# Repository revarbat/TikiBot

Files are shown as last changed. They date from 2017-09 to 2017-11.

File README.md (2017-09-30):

TikiBot
=======
Touchscreen BarBot software for auto-dispensing mixed drinks.  Runs under
Linux on a Raspberry Pi or Udoo, using DC motor controllers over I2C, to
activate pumps and valves to dispense ingredients.

TikiBot Lives!  It was a great success at my friend's Tiki themed party.

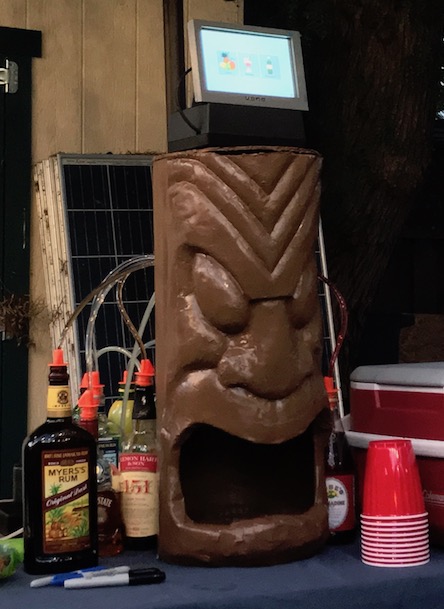
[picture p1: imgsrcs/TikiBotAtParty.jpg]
TikiBot Live at a Party


Standard Drinks List
--------------------
The default configuration is for a 12-feed TikiBot.
It expects the following ingredient feeds:

1. Meyer's Dark Rum
2. Appleton's Signature Blend
3. Meyer's Platinum White Rum
4. Lemonheart 151 Rum
5. Lime Juice
6. Lemon Juice
7. Orange Juice
8. Pineapple Juice
9. Passion Fruit Syrup
10. Sugar Syrup
11. Angostura Bitters
12. Grenadine

The following Tiki recipes can be made from those:

1. Beachcomber's Gold
2. Chief Lapu Lapu
3. Hurricane
4. Planter's Punch
5. Shrunken Skull
6. Tiger Shark
7. Trader Vic Grog
8. Zombie

The following non-alcoholic juice drinks can also be made:

1. Orange Juice
2. Pineapple Juice
3. Pineapple Orange Juice
4. Tropical Punch

Hardware
--------
This software has been tested with the following hardware:

- Udoo Neo ( [Udoo.org](https://www.udoo.org) )
- 7" 800x480 Touchscreen HDMI display
- 3 Adafruit DC Motor Featherwings ( [Adafruit.com](https://www.adafruit.com/product/2927) )
- 12 Small self-priming pumps ( [TrossenRobotics.com](http://www.trossenrobotics.com/robotgeek-pump-small) )
- 12 Normally Closed solonoid valves ( [Amazon.com](https://www.amazon.com/dp/B007D1U64E/ref=cm_sw_r_tw_dp_x_qDVWzbPCEW4K5) )

Each DC Motor controller handles up to 4 feeds.  Each motor controller will
need to have a consecutive different I2C address. You can alternately use
the following DC motor controllers without changing any code:

- Adafruit DC & Stepper Motor HAT for Raspberry Pi ( [Adafruit.com](https://www.adafruit.com/product/2348) )
- Adafruit Motor/Stepper/Servo Shield for Arduino v2 ( [Adafruit.com](https://www.adafruit.com/product/1438) )

It should be trivial to use a Raspberry Pi instead of the Udoo Neo.
Probably the easiest configuration would be to use a Raspberry Pi
with a few stacked DC Motor HATs.

Each feed is a paired pump and valve, wired in parallel.
Each pump/valve combo should be wired and plumbed as follows:

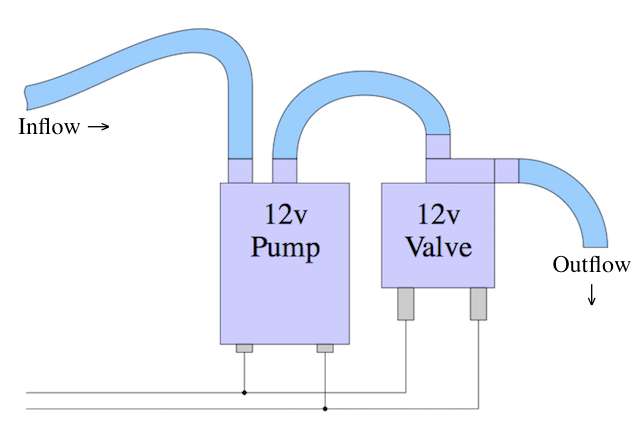
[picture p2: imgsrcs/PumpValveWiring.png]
Pump/Valve wiring


The polarity of the wiring is irrelevant for the linked pumps and
valves.  For them, either polarity will result in the forward pump
action with the valve open.

The pumps-valve pairs can be seated into a ring of Pump Wedges that can
be 3D printed from the model `STLs/PumpWedge12.stl` (for a 12 feed ring)
or `STLs/PumpWedge16.stl` (for 16 feed rings).  A corresponding Feed Guide
model can be found as `STLs/FeedGuide12.stl` or `STLs/FeedGuide16.stl`.
The feed guide has a slot in the bottom that can hold a funnel for all
the feeds to pour and mix into, which will drain into the target glass
or cup.

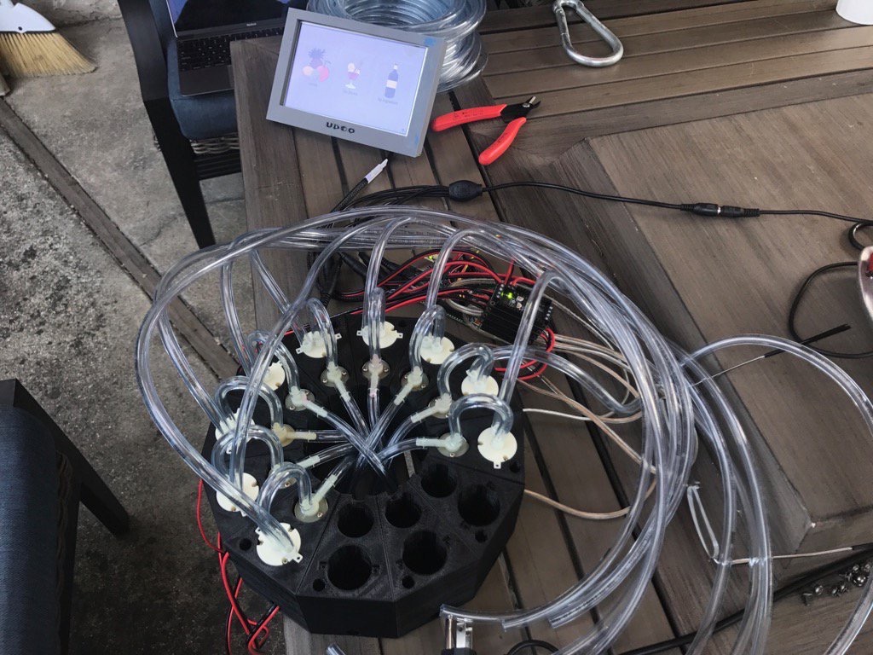
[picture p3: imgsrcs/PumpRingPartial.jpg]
Pump/Valve Ring, Partially Completed


Installation
------------

    unzip TikiBot.zip
    cd TikiBot
    pip3 install -r requirements.txt

Running TikiBot
---------------
`gui.py` is the main file to run to launch this application.  You will
need to run it using Python 3.6 or better.

     cd TikiBot/TikiBot
     python3 gui.py

Configuration
-------------
The file `TikiBot/resources/tikibot_configs.yaml`: Contains all configs
for passcode, feeds, recipes, etc. for a standard set of Tiki drinks.
On first run, if you edit any configs on the configuration screen,
these configs will be written out to the file `$HOME/.tikibot.yaml`,
which will be read in all future runs.

In the lower right corner of the main screen is a gear icon.  This is
the configuration menu button. If you press it, it will ask for an
administrative passcode.  The default is '8888'.  Once you enter the
correct passcode, you will be shown the configuration screen.  From
here, you can change the passcode (recommended!), add, edit and re-order
feeds, add, and edit drink recipes, and shutdown or reboot the system.
Any changes made here will be saved to the `$HOME/.tikibot.yaml` file.

Calibration
-----------

1. Enter the configuration screen as described above.

2. In the configuration screen, the `Manage Feeds` button will show you
    all of the feeds that the software expects, in the order that it
    expects them.

3. Take an empty cup and zero a gram scale with it on it.  Make sure the
    scale is set to measure grams.

4. Select a feed, and you will be presented with a screen that will let
    you rename it, enable/disable it, start and stop it manually, and
    calibrate it.

5. Make sure that the feed line you selected has the expected ingredient
    attached.

6. Place the cup under the output of the feed.

7. Press the `Start Feed` button to prime the feedline.

8. When fluid starts pouring into the cup, press the `Stop Feed` button.

9. Pressing the calibration button will show you a screen which will let
    you calibrate the flow rate and pulse overage for that feed.

10. Start with a Pulse overage of 0.2 and a Duty cycle of 100%.  Those
    are only really needed for advanced calibration.  Select an amount
    of 25 milliliters to dispense.  A flow rate of 12.0 is a reasonable
    starting place.

11. Empty the cup and re-zero the scale with the empty cup.

12. Place the cup back under the output of the feed.

13. Press `Pour` to dispense into the cup.  Wait for it to finish dispensing.

14. Weigh the cup, to see how many grams of fluid were dispensed.

15. Take the number of grams measured, divide it by the expected number of
    milliliters dispensed (25mL, if you followed the above instructions),
    then multiply that by the current `Flow` setting.  Change the `Flow`
    to this new value.

    `newflow = oldflow * dispensed / expected`

    Note: You can expect viscous fluids like Sugar Syrup to have very low
    flow rates like 2.5 mL/s.

16. Repeat steps 11 to 15 a couple times until the amount dispensed is
    within about a gram of the expected amount.

17. Press the back arrow button to get back to the feeds listing screen.

18. Select the next feed button and go back to step 3.  Repeat until all
    feeds have been calibrated.

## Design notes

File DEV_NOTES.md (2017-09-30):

Developer Notes
===============

Screens Concept
---------------
The touchscreen user interface is based around the idea of a stack
of screens, something like old HyperCard.

- `screen_push(newscreen)`:
    pushes a new screen onto the stack.

- `screen_pop()`:
    pops the topmost screen off of the stack.

- `activate()`:
    This method called on a screen class when that screen
    becomes the topmost screen, either through push or pop.
    This allows for updating the content of the screen after
    another screen has been popped off the top of the stack.

Touchscreen Widgets
-------------------
These are widgets that can be used in the creation of a screen.

- RectButton
    Provides a rectangular button on all platforms.

- TouchCheckbox:
    Provides a slider-switch visual version of the standard
    CheckButton.  Slightly prettier and more touchscreen friendly.

- TouchSpinner:
    Provides a basic increment/decrement Spinner widget that is
    more touchscreen friendly.

Generic Screens
---------------
There's a few generic screens that are used in multiple places:

- SelectScreen:
    Given a list of strings, shows buttons for each one, with
    a callback that gets passed the text of the button pressed.
    This is sometimes used as a confirmation screen by just giving
    it a ["Confirm"] button and a text message to display.

- AlphaScreen:
    Provides a touchscreen keyboard for text entry and editing.

- ListScreen:
    Provides a way to edit a list of arbitrary size, through callbacks.
    Can add, delete, edit, and re-order items with standard buttons.

- NotifyScreen:
    Displays a message for the user to see and dismiss.

- LockScreen:
    Dispays a numeric keypad to allow entry or setting of keycodes.

Screens Layout
--------------
Here's the hierarchy of GUI screens for the application.  The button
name that leads to a screen is in "quotes".  If a screen is a
subclass of another screen class, the base class is in (parens).

    MainScreen
        "Juices" RecipeScreen(SelectScreen)
            PourScreen
                "Pour" DispensingScreen
        "Tiki Drinks" RecipeScreen(SelectScreen)
            PourScreen
                "Pour" DispensingScreen
        "By Ingredient" ByIngredientScreen(SelectScreen)
            PourScreen
                "Pour" DispensingScreen
        "⚙" LockScreen
            ConfigScreen
                "Manage Feeds" ManageFeedsScreen(ListScreen)
                    "+" AlphaScreen
                        "Select" FeedEditScreen
                            "Rename Feed" AlphaScreen
                            "Calibrate" CalibScreen
                    "-" SelectScreen
                    "✎" FeedEditScreen [see above]
                "Manage Recipes" ManageRecipesScreen(ListScreen)
                    "+" AlphaScreen
                        "Select" RecipeEditScreen
                            "Recipe:" AlphaScreen
                            "Category:" AlphaScreen
                            "+" SelectScreen
                            "-" SelectScreen
                            "✎" AmountScreen
                    "-" SelectScreen
                    "✎" RecipeEditScreen [see above]
                "Dump All Feeds" DumpScreen
                "Change Passcode" LockScreen
                    NotifyScreen
                "Shutdown" ShutdownScreen

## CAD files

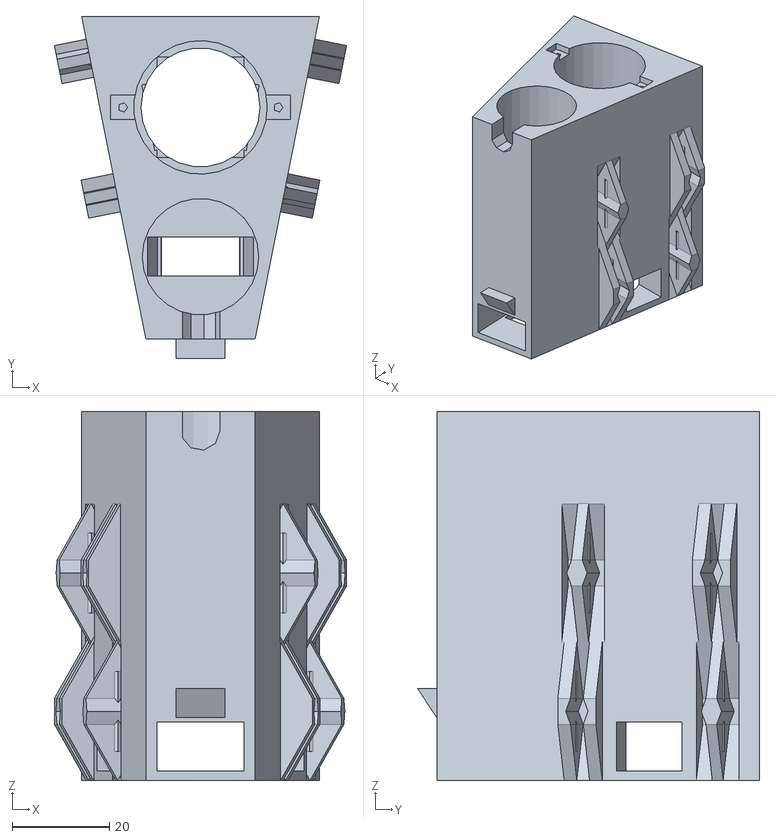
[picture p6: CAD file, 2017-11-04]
STLs/PumpWedge16.stl
60.2 x 70.5 x 76.0

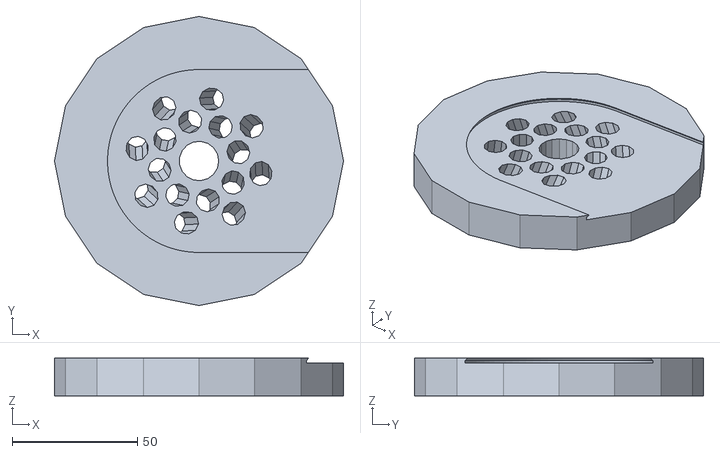
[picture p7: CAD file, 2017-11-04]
STLs/FeedGuide16.stl
115.3 x 115.3 x 15.0

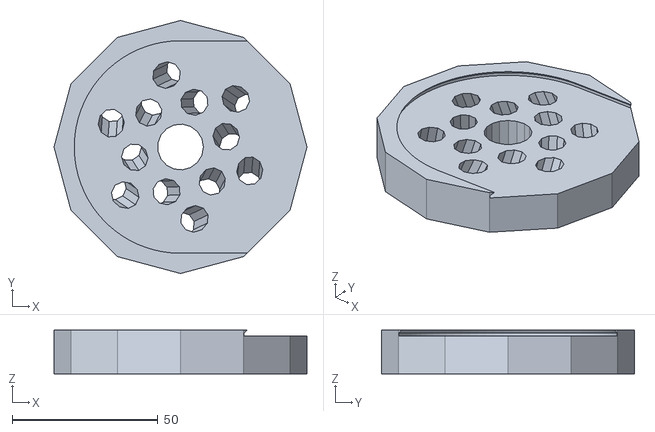
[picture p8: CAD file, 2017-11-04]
STLs/FeedGuide12.stl
86.9 x 86.9 x 15.0

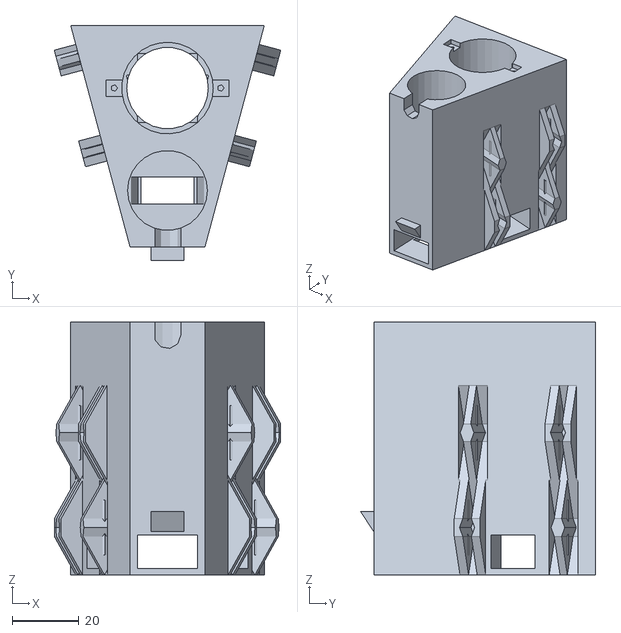
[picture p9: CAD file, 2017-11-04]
STLs/PumpWedge12.stl
68.0 x 70.5 x 76.0

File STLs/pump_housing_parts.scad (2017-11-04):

use <BOSL/transforms.scad>
use <BOSL/shapes.scad>
use <BOSL/joiners.scad>


/* [General] */

// Which part to print.
parts = "feedguide"; // [assembled:Full Assembly,feedguide:Output Feed Guide,ringseg:Ring Segment,stand:Standoff Pillars]

// Thickness of walls in mm.
wall_thick = 5; // [2:0.5:10]

// Number of pumps in the ring.
pump_count = 12; // [4:1:24]

tubing_diam = 9;

stand_height = 200;


/* [Pump] */

// Diameter of pump body, in mm.
pump_diam = 27.5; // [20:0.5:75]

// Diameter of pump inlet, in mm.
pump_inlet_diam = 8; // [3:0.5:10]

// Diameter of pump outlet, in mm.
pump_outlet_diam = 8; // [3:0.5:10]

// Offset of pump outlet, in mm.
pump_outlet_offset = 9.5; // [3:0.5:35]

// Offset of pump outlet, in mm.
pump_outlet_angle = 0; // [0:15:345]

// Length of pump, in mm.
pump_length = 61.0; // [20:0.5:100]

// Size of pump screws in mm.
pump_screw_size = 2.0; // [2:5]

// Size of pump screws in mm.
pump_screw_spacing = 32.0; // [20:0.5:75]


/* [Valve] */

// Diameter of valve body, in mm.
valve_diam = 24; // [16:0.5:75]

// Diameter of valve inlet, in mm.
valve_inlet_diam = 8; // [3:0.5:10]

// Diameter of valve outlet, in mm.
valve_outlet_diam = 8; // [3:0.5:10]

// Offset of valve outlet, in mm.
valve_outlet_offset = 9.5; // [3:0.5:35]

// Offset of valve outlet, in mm.
valve_outlet_angle = 0; // [0:15:345]

// Length of valve, in mm.
valve_length = 37.0; // [20:0.5:100]




/* [Hidden] */

pi = 3.141592653589793236;

slop = 0.2;


$fa = 3;
$fs = 3;


wedge_height = max(pump_length, valve_length) + wall_thick + 10;
wedge_width = max(pump_diam, valve_diam) - wall_thick;
wedge_depth = pump_diam+valve_diam+3*wall_thick;

module pump_housing_ring_segment()
{
	h = wedge_height;
	w = wedge_width;
	d = wedge_depth;
	ow = w + d * 2 * tan(360/pump_count/2);
	joiner_height = h * 0.75;
	union() {
		difference() {
			union() {
				// Main wedge shape.
				up(h/2) xrot(-90) trapezoid([w, h], [ow, h], h=d, center=true);

				// Feed guide support
				up(10+2+1) fwd(d/2) trapezoid([10, 0.1], [10, 2*4], h=6, center=false);
			}

			// side joiner clearing
			up(joiner_height/2) {
				yrot_copies([0, 180]) {
					right(w/2) {
						fwd(d/2) {
							zrot(-360/pump_count/2) {
								back(d/2-wall_thick/2) {
									zrot(90) joiner_clear(h=joiner_height, w=8, clearance=1);
									back(d/2-wall_thick) zrot(-90) yrot(180) joiner_clear(h=joiner_height, w=8, clearance=1);
								}
							}
						}
					}
				}
			}

			// radial wiring holes
			up(2) upcube([valve_diam-2*3, d+1, 10], center=true);

			// Pump hole
			back(d/2-pump_diam/2-wall_thick) {
				// Diametral wiring holes
				up(2) {
					xflip_copy() {
						zrot(360/pump_count/2) {
							left(ow/2) upcube([ow, pump_diam/2, 10]);
							left(pump_diam/2-4) {
								up(10-0.01) trapezoid([2*3, pump_diam/2], [0.1, pump_diam/2], h=5, center=false);
							}
						}
					}
				}

				// radial wiring hole taper
				up(10+2-0.01) trapezoid([valve_diam-2*3, pump_diam-2], [valve_diam-2*3, pump_diam-2*5], h=5, center=false);

				// Pump Body hole
				up(h-pump_length+0.01) {
					cylinder(h=pump_length, d=pump_diam, center=false);
					cylinder(h=h*3, d=pump_diam-3, center=true);
				}

				// Pump Tabs
				up(h-2+0.01) {
					xspread(pump_screw_spacing) {
						upcube([pump_screw_size*2.5, pump_screw_size*2.5, 2]);
					}
				}

				// Pump tab screw holes
				up(h-15+0.01) {
					xspread(pump_screw_spacing) {
						cylinder(d=pump_screw_size, h=16, center=false);
					}
				}
			}

			// Valve hole
			fwd(d/2-valve_diam/2-wall_thick) {
				// Valve body hole and shelf.
				up(h-valve_length+0.01) cylinder(h=valve_length, d=valve_diam, center=false);
				down(0.01) trapezoid([valve_diam-8, 10], [valve_diam-2, 8], h=h-valve_length+1, center=false);

				// Valve output clearance
				up(h-valve_outlet_diam/2) {
					up(5/2) {
						hull() {
							zspread(5) {
								xrot(90) cylinder(d=valve_outlet_diam, h=valve_diam, center=false);
							}
						}
					}
				}
			}
		}

		// Side Joiners
		up(joiner_height/2) {
			yrot_copies([0,180]) {
				right(w/2) {
					fwd(d/2) {
						zrot(-360/pump_count/2) {
							back(d/2-wall_thick/2) {
								zrot(-90) joiner(h=joiner_height, w=8, l=6);
								back(d/2-wall_thick) zrot(-90) yrot(180) joiner(h=joiner_height, w=8, l=6, slop=slop);
							}
						}
					}
				}
			}
		}
	}
}
//!pump_housing_ring_segment();



module pump_housing_feed_guide()
{
	h = 15;
	w = wedge_width;
	d = wedge_depth;
	funnel_diam = 75;
	r = w / 2 / sin(180/pump_count);
	difference() {
		// Main body.
		cylinder(r=r, h=h, center=false, $fn=pump_count);

		// Central stacking bank bypass.
		cylinder(d=tubing_diam*1.75, h=h*3, center=true);

		// Inner ring of feeds.
		zring(n=pump_count/2, r=tubing_diam*2.0) {
			yrot(-10) xrot(-15) cylinder(d=tubing_diam, h=h*3, center=true);
		}

		// Outer ring of feeds.
		zrot(360/(pump_count/2)/2) {
			zring(n=pump_count/2, r=tubing_diam*3.0) {
				yrot(-10) xrot(-20) cylinder(d=tubing_diam, h=h*3, center=true);
			}
		}

		// funnel groove
		hull() {
			grid_of(xa=[0, 2*r]) {
				up(h-2) {
					cylinder(h=1.01, d=funnel_diam, center=false);
					up(1) cylinder(h=1.01, d1=funnel_diam, d2=funnel_diam-2*1, center=false);
				}
			}
		}
	}
}



module pump_housing_stand()
{
	h = stand_height * ((stand_height>150)? 0.5 : 1.0);
	w = wedge_width;
	d = wedge_depth;
	joiner_height = h * 0.75;
	union() {
		difference() {
			union() {
				cylinder(h=h, d=pump_diam+6, center=false);
				cylinder(h=h+12, d=pump_diam-3-slop, center=false);
			}
			down(0.01) {
				cylinder(h=h*2, d=pump_diam-10, center=false);
				difference() {
					cylinder(h=h-10+0.02, d=pump_diam-3, center=false);
					upcube([10-slop, d, 10-slop]);
				}
				up(h-10) {
					cylinder(h=7, d1=pump_diam-3, d2=pump_diam-10, center=false);
				}
			}
			up(10/2-0.01) {
				xrot(-90) upcube([10, 10, d]);
			}
			up(h) {
				upcube([10-slop, d, 20]);
			}
		}
	}
}



module pump_housing_parts() { // make me
	h = wedge_height;
	w = wedge_width;
	d = wedge_depth;
	r = w / 2 / sin(180/pump_count) + d/2;
	if (parts == "assembled") {
		zring(r=r, n=pump_count, rot=true) {
			zrot(-90) pump_housing_ring_segment();
		}
		up(22+10+2+1) {
			zrot(360/pump_count/2) yrot(180) pump_housing_feed_guide();
		}
	} else if (parts == "ringseg") {
		pump_housing_ring_segment();
	} else if (parts == "feedguide") {
		pump_housing_feed_guide();
	} else if (parts == "stand") {
		pump_housing_stand();
	}
}



pump_housing_parts();



// vim: noexpandtab tabstop=4 shiftwidth=4 softtabstop=4 nowrap

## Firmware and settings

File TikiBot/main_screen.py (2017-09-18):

try:  # Python 2
    from Tkinter import *  # noqa
except ImportError:  # Python 3
    from tkinter import *  # noqa

import math
from recipes import Recipe
from rectbutton import RectButton
from recipe_screen import RecipeScreen
from lock_screen import LockScreen
from config_screen import ConfigScreen
from byingredient_screen import ByIngredientScreen


class MainScreen(Frame):
    def __init__(self, master):
        super(MainScreen, self).__init__(master, class_="MainScreen")
        self.master = master
        self.buttons = []
        self.update_buttons()

    def update_buttons(self):
        for btn in self.buttons:
            btn.forget()
            btn.destroy()
        types = Recipe.getTypeNames()
        colsarr = [1, 2, 3, 2, 3, 3, 4]
        maxcols = colsarr[len(types)]
        col, row = 1, 1
        for type_ in types:
            img = self.master.get_image(Recipe.getTypeIcon(type_))
            cmd = lambda typ=type_: self.handle_type_button(typ)
            btn = Button(self, text=type_, compound=TOP, image=img, command=cmd, width=160)
            btn.grid(column=col, row=row, padx=5, pady=5)
            self.buttons.append(btn)
            col += 1
            if col > maxcols:
                col = 1
                row += 1
                self.rowconfigure(row, weight=0)
        img = self.master.get_image("IngredientsIcon.gif")
        btn = Button(self, text="By Ingredient", compound=TOP, image=img, command=self.handle_button_ingredients, width=160)
        btn.grid(column=col, row=row, padx=5, pady=5)
        self.buttons.append(btn)
        confbtn = RectButton(self, text="\u2699", command=self.handle_button_conf, width=15, height=20)
        confbtn.grid(column=maxcols, row=row, columnspan=2, rowspan=2, sticky=S+E)
        self.buttons.append(confbtn)
        self.columnconfigure(0, weight=1)
        for col in range(maxcols):
            self.columnconfigure(col+1, weight=0)
        self.columnconfigure(maxcols+1, weight=1)
        self.columnconfigure(maxcols+2, weight=0)
        self.columnconfigure(maxcols+3, weight=0)
        self.rowconfigure(0, weight=1)
        self.rowconfigure(1, weight=0)
        self.rowconfigure(row+1, weight=1)
        self.rowconfigure(row+2, weight=0)
        self.rowconfigure(row+3, weight=0)

    def activate(self):
        self.update_buttons()

    def handle_type_button(self, type_):
        recipes = Recipe.getRecipesByType(type_)
        self.master.screen_push(RecipeScreen(self.master, recipes, "Choose one of these %s:" % type_))

    def handle_button_ingredients(self):
        self.master.screen_push(ByIngredientScreen(self.master))

    def handle_button_conf(self):
        self.master.screen_push(LockScreen(self.master, ConfigScreen(self.master)))

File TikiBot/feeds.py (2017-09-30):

import sys
import time
import platform
import operator

from Adafruit_MotorHAT import Adafruit_MotorHAT as AFMH
from Adafruit_GPIO.I2C import get_i2c_device


progstart_time = time.time()


def eprint(*args, **kwargs):
    print(*args, file=sys.stderr, **kwargs)


class SupplyFeed(object):
    motor_controllers = {}
    dc_motors = {}
    max_motor_num = 0
    feed_order = []
    feeds = {}
    feed_types = {}

    def __init__(self, type_, name, flowrate=14.2, overage=0.25, proof=0, avail=True):
        if type_ not in SupplyFeed.feed_types:
            SupplyFeed.feed_types[type_] = []
        SupplyFeed.feed_types[type_].append(self)
        self.type_ = type_
        self.name = name
        self.flowrate = flowrate
        self.pulse_overage = overage
        self.proof = proof
        self.flowing = False
        self.avail = avail
        self.motor_num = SupplyFeed.max_motor_num
        self.motor = None  # Defer instantiation for cross-platform debugging
        SupplyFeed.max_motor_num += 1
        SupplyFeed.feeds[name] = self
        SupplyFeed.feed_order.append(self)

    @classmethod
    def fromDict(cls, d):
        """Create new SupplyFeed instances from a dictionary description."""
        # Delete old feeds
        for feed in cls.feed_order:
            feed.delete_feed()
        # Add feeds from dict
        for feeddict in d['feeds']:
            for name, data in feeddict.items():
                cls(
                    data.get('type', 'Juices'),
                    name,
                    flowrate=data.get('flowrate', 14.2),
                    overage=data.get('overage', 0.25),
                    proof=data.get('proof', 0),
                    avail=data.get('available', True)
                )

    @classmethod
    def toDictAll(cls, d):
        """Create a dictionary description of all SupplyFeed instances."""
        d['feeds'] = []
        for feed in cls.feed_order:
            d['feeds'].append(feed.toDict())
        return d

    def toDict(self):
        """Create a dictionary description of this SupplyFeed instance."""
        return {
            self.name: {
                'type': self.type_,
                'flowrate': self.flowrate,
                'overage': self.pulse_overage,
                'proof': self.proof,
                'available': self.avail,
            }
        }

    @classmethod
    def _getMotorByNumber(cls, motor_num):
        """Returns the DCMotor instance for the given motor number."""
        addr = 0x60 + motor_num // 4
        num = motor_num % 4
        if addr not in cls.motor_controllers:
            busnum = 0
            if platform.system() == "Linux":
                if "udooneo" in platform.release():
                    busnum = 1
            cls.motor_controllers[addr] = AFMH(addr, i2c_bus=busnum)
        if motor_num not in cls.dc_motors:
            cls.dc_motors[motor_num] = cls.motor_controllers[addr].getMotor(num + 1)
        return cls.dc_motors[motor_num]

    @classmethod
    def getTypeNames(cls):
        """Returns a sorted string list of all SupplyFeed types."""
        return sorted(cls.feed_types.keys())

    @classmethod
    def getFeedsByType(cls, name):
        """Returns a list of all SupplyFeeds of a given type, sorted by name."""
        feed_list = cls.feed_types[name]
        return sorted(feed_list, key=operator.attrgetter('name'))

    @classmethod
    def getNames(cls):
        """Returns a sorted list of the names of all SupplyFeeds."""
        return sorted(cls.feeds.keys())

    @classmethod
    def getAll(cls):
        """Returns a list of all SupplyFeeds, sorted by name."""
        for key in sorted(cls.feeds.keys()):
            yield cls.feeds[key]

    @classmethod
    def getAllOrdered(cls):
        """Returns a list of all SupplyFeeds, sorted by feed number."""
        return cls.feed_order

    @classmethod
    def getByName(cls, name):
        """Get a SupplyFeed instance by name."""
        return cls.feeds[name]

    def getName(self):
        """Get the name of this SupplyFeed instance."""
        return self.name

    def isFlowing(self):
        """Returns true if this SupplyFeed if currently on/flowing."""
        return self.flowing

    def startFeed(self):
        """Turn on this SupplyFeed, to start it flowing."""
        if platform.system() == "Linux":
            # turn on solonoid/motor for feed
            if self.motor is None:
                self.motor = SupplyFeed._getMotorByNumber(self.motor_num)
            self.motor.setSpeed(255)
            self.motor.run(AFMH.FORWARD)
        else:
            eprint("Starting feed %d @%f" % (self.motor_num, time.time() - progstart_time))
        self.flowing = True

    def stopFeed(self):
        """Turn off this SupplyFeed, to stop it's flow."""
        if platform.system() == "Linux":
            # turn off solonoid/motor for feed
            if self.motor is None:
                self.motor = SupplyFeed._getMotorByNumber(self.motor_num)
            self.motor.setSpeed(0)
            self.motor.run(AFMH.RELEASE)
        else:
            eprint("STOPPING feed %d @%f" % (self.motor_num, time.time() - progstart_time))
        self.flowing = False

    def delete_feed(self):
        """Delete this SupplyFeed, removing it from the feed_order, feeds, and feed_types"""
        del SupplyFeed.feeds[self.name]
        SupplyFeed.feed_types[self.type_].remove(self)
        if not SupplyFeed.feed_types[self.type_]:
            del SupplyFeed.feed_types[self.type_]
        SupplyFeed.feed_order.remove(self)
        SupplyFeed.max_motor_num -= 1
        for n, feed in enumerate(SupplyFeed.feed_order):
            feed.motor_num = n

    def rename(self, newname):
        """Change the name of this SupplyFeed."""
        del SupplyFeed.feeds[self.name]
        self.name = newname
        SupplyFeed.feeds[newname] = self

    def retype(self, newtype):
        """Change the type of this SupplyFeed."""
        SupplyFeed.feed_types[self.type_].remove(self)
        if not SupplyFeed.feed_types[self.type_]:
            del SupplyFeed.feed_types[self.type_]
        self.type_ = newtype
        if newtype not in SupplyFeed.feed_types:
            SupplyFeed.feed_types[newtype] = []
        SupplyFeed.feed_types[newtype].append(self)

    @classmethod
    def transpose(cls, pos):
        """Transpose the given feed with the one after it in the feed order, swapping their motor_num's."""
        if pos >= 0 and pos < len(cls.feed_order)-1:
            cls.feed_order[pos:pos+2] = reversed(cls.feed_order[pos:pos+2])
            for n, feed in enumerate(cls.feed_order):
                feed.motor_num = n

    def getOrder(self):
        """Returns the ordinal position of this feed in the feed order.  0-based."""
        return SupplyFeed.feed_order.index(self)
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

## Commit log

2017-09-18 Added system reboot feature.
    [shutdown_screen.py]
2017-09-19 Fixed busnum param to be i2c_bus
    [feeds.py]
2017-09-21 Added pump/valve wiring diagram.
2017-09-21 Adjusted Pump/Valve wiring image size
2017-09-22 Small addition to wiring description.
2017-09-22 Added STLs for making pump rings.
    [FeedGuide12.stl, FeedGuide16.stl, PumpWedge12.stl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]
2017-09-22 Fixed some LockScreen layout issues.
    [gui.py, lock_screen.py]
2017-09-22 Fixed clipping of LockScreen label text.
    [lock_screen.py]
2017-09-24 Fixed dispensing timeslicing for heterogenous flow rates.
    [recipes.py]
2017-09-26 Make switch images nicer.
2017-09-27 Added Calibration section to README
2017-09-28 Fixed motor_number re-ordering in delete_feed()
    [feeds.py]
2017-11-04 Updated STL models.
    [FeedGuide12.stl, FeedGuide16.stl, PumpWedge12.stl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]
